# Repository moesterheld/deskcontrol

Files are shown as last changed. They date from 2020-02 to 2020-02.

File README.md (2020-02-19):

# myDeskControl Steuerung
## Wofür ist myDeskControl?
myDeskControl ist eine Arduino basierte Erweiterung für Assmann Sympas Steh-Sitz-Tische. Sie wird zwischen die Steuerknöpfe am Tisch und die Steuereinheit unter dem Tisch geschaltet und kann so die Steuerung des Motors automatisieren. Durch Nutzung eines Ultraschalldistanzsensors können so eine Position für Oben und Unten gespeichert und angesteuert werden. 
## Wie wird myDeskControl benutzt?
An die myDeskControl Einheit wird das bestehende Anschlusskabel der Steuerungsknöpfe angeschlossen um auf Tastendrücke reagieren zu können. Die Tastendrücke werden dann verarbeitet und über ein an die bestehende Buchse der Steuereinheit des Motors angeschlossenes Netzwerkkabels die notwendigen Aktionen ausgeführt.
Dabei können folgende Funktionen über die Tasten angesteuert werden:
- Langer Druck auf :heavy_plus_sign: / :heavy_minus_sign: : Tisch auf- / abfahren (entspricht der Standardfunktion)
- Druck auf :heavy_plus_sign: direkt gefolgt von einem Druck auf :heavy_minus_sign: : Aktuelle Position als "Oben" Position speichern
- Druck auf :heavy_minus_sign: direkt gefolgt von einem Druck auf :heavy_plus_sign: : Aktuelle Position als "Unten" Position speichern
- Kurzer Druck auf :heavy_plus_sign: / :heavy_minus_sign: : Tisch automatisch zu gespeicherter Position auf- / abfahren
- Durch den Druck auf eine der Tasten während der automatischen Fahrt kann die Fahrt gestoppt oder eine automatische Fahrt in die andere Richtung ausgelöst werden.  
## Wie funktioniert myDeskControl?
myDeskControl verwendet als zentrales Bauteil einen Arduino (kompatiblen) Mikroprozessor. 
Da die Steuertasten des Tisches über ein RJ45 Kabel an der Tischsteuerung angeschlossen sind, kann der Anschluss zur Erkennung am Mikroprozessor relativ einfach erfolgen. 
Zur Positionsmessung ist ein Ultraschallsensor am Mikroprozessor angeschlossen, der bei Bedarf die aktuelle Entfernung zum Boden misst.  
Aus Tastendruck und aktueller Position kann der Prozessor berechnen, welche Aktion zum Erreichen der gewünschten Funktionalität notwendig ist. Diese Aktion wird durch eine Simulation des Tastendrucks ausgeführt.
Die Tastendrücke zum Hoch-/Runterfahren des Tisches werden durch je einen Optokoppler der das Signal dann wieder über ein RJ45 Kabel an die Steuereinheit überträgt simuliert.
Durch Betätigen beider Tasten gleichzeitig kann die aktuelle Position als Oben-/Unten-Position persistent im EEPROM des Mikroprozessors gespeichert werden und steht so auch noch zur Verfügung nachdem die myDeskControl vom Strom getrennt wurde.  
Eine maximale Fahrzeit in eine Richtung dient als Sicherungsfunktion um nicht unter Umständen (z.B. bei Defekt eines der Tasten) unkontrolliert in eine Richtung zu fahren. Alle weiteren von Werk integrierten Sicherungsfunktionen des Tisches (Maximalhöhe / Blockierungsschutz) bleiben erhalten.
## Wie kann ich mir mein eigenes myDeskControl bauen?
Für den Bau des myDeskControl werden benötigt:
- 1x [Wemos D1 Mini ESP8266-12F Mikroprozessor](https://amzn.to/37IjiAW)
- 1x [HC-SR04 Ultraschall Sensor](https://amzn.to/37GAg2z)
- 2x [RJ45 Buchse](https://amzn.to/2udEeCb)
- 2x [PC817 Optokoppler](https://amzn.to/2HF5MmR)
- 4x 220&#8486; Widerstand
- 4x 10k&#8486; Widerstand
- 2x LEDs
- 1x passende Lochrasterplatine oder alternativ die von aisler.com produzierte Platine aus dem Fritzing Entwurf.

Aus Platz- und Kostengründen wird für das veröffentlichte Projekt auf einen Wemos D1 Mini ESP8266 Mikroprozessor zurückgegriffen. Die Funktionalität kann aber für jeden Arduino-kompatiblen Mikroprozessor angepasst werden.

Auf die beiden LEDs sowie zwei der zugehörigen 220&#8486; Vorwiderstände kann verzichtet werden. Sie dienen lediglich der optischen Anzeige der aktuell betätigten Fahrtrichtung. Zusätzlich wird das Speichern der Position als Blinken angezeigt.

Der Anschluss erfolgt gemäß dem [Fritzing Entwurfs](DeskControlDeluxe.fzz) als Prototyp

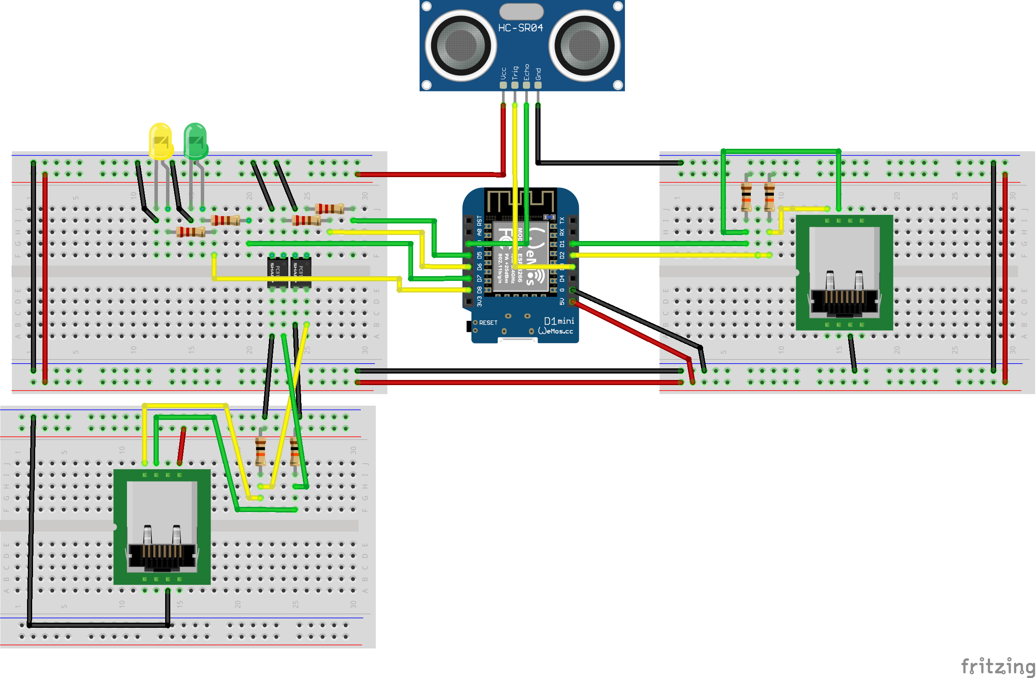
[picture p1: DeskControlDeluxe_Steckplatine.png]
Prototype


oder auf der Leiterplatte

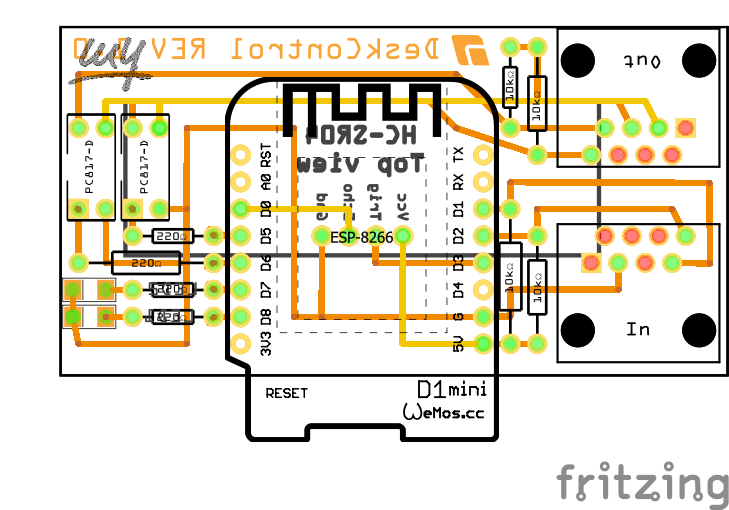
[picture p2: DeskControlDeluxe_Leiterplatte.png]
Leiterplatte


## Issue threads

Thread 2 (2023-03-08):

Research Protokoll hinterer RJ45

peteh, 2023-03-08:
Hi,

mein Tisch hat 2 RJ45 Stecker, kann man darueber auch komplexere Befehle senden oder ist das ganze wirklich nur ein Mapping auf digitale IOs?
Es gibt ein Tool von OMT, mit dem man den Tisch auch per USB  vom PC kontrollieren kann.

moesterheld, 2023-03-08:
Hi @peteh, ich hatte nur die einfachen Auf-/Ab Schalter zur Verfügung und festgestellt, dass sie ganz gewöhnliche Schalter, die über die drei Adern im RJ45 schalten. Das habe ich mir damals für das Projekt zunutze gemacht.
Ich denke aber schon, dass man damit auch komplexer steuern könnte, wenn man ein "richtiges" Steuergerät reengineeren würde oder die Specs kennen würde. Da kann ich aber leider nicht weiterhelfen, da mir das abgeht und ich mittlerweile nicht einmal mehr Zugriff auf einen dieser Tische habe.

Closed 2023-03-08.

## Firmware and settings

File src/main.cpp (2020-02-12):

#include <Arduino.h>
#include <EEPROM.h>
#include <MyUltrasoundSensor.h>

// pins
int BUTTON_UP = D1;   // pull-up !
int BUTTON_DOWN = D2; // pull-up !
int US_TRIGGER = D3;
int US_ECHO = D0;
int OUTPUT_UP = D6;
int OUTPUT_DOWN = D5;
int LED_UP = D7;
int LED_DOWN = D8;

// variables for button logic
enum direction {
  NONE, UP, DOWN
};
enum mode {
  MANUAL, AUTOMATIC
};
direction initialDirection = NONE;
bool buttonPressed = false;
bool buttonLongPressed = false;
bool positionStored = false;
uint32_t  buttonTimer = 0;
uint32_t  longPressTimeout = 1000;

// variables for driving desk
MyUltrasoundSensor uss(US_TRIGGER, US_ECHO);
int lastPosition;
int positionUp;
int positionDown;
int EEPROM_UP = 0;
int EEPROM_DOWN = 1;
direction drivingDirection = NONE;
mode drivingMode = MANUAL;
uint32_t  drivingTimer = 0;
uint32_t  drivingTimeout = 20000;

// stop driving desk
void stopDesk() {
  Serial.println("Stopping desk");
  // stop motor
  digitalWrite(OUTPUT_UP, LOW);
  digitalWrite(LED_UP, LOW);
  digitalWrite(OUTPUT_DOWN, LOW);
  digitalWrite(LED_DOWN, LOW);
  drivingDirection = NONE;
  drivingMode = MANUAL;
}

// start driving desk in direction
void driveDesk(direction dir) {
  // drive motor in direction (stop going the other way first)
  if (drivingDirection != NONE && drivingDirection != dir) {
    stopDesk();
  }
  if (drivingDirection == NONE) {
    drivingTimer = millis();
  }
  if (drivingDirection == dir) {
    return;
  }
  if (dir == UP) {
    Serial.println("Driving desk up");
    digitalWrite(OUTPUT_UP, HIGH);
    digitalWrite(LED_UP, HIGH);
    drivingDirection = UP;
  } else {
    Serial.println("Driving desk down");
    digitalWrite(OUTPUT_DOWN, HIGH);
    digitalWrite(LED_DOWN, HIGH);
    drivingDirection = DOWN;
  }
}

// start autodriving desk to position
void autoDriveDesk(direction dir) {
  // auto drive desk to position, stop motor if already going in that direction
  if (drivingDirection != NONE && drivingDirection == dir) {
    stopDesk();
    return;
  } 

  if ((dir == UP && lastPosition >= positionUp) || (dir == DOWN && lastPosition <= positionDown)) {
    Serial.println("Not driving desk. Already in position.");
    return;
  }

  Serial.print("Driving desk to position ");
  if (dir == UP) {
    Serial.println("UP");
  } else {
    Serial.println("DOWN");
  }
  drivingMode = AUTOMATIC;
  driveDesk(dir);
}

void blink(int ledPin) {
  for (int i=0; i<3; i++) {
    digitalWrite(ledPin, HIGH);
    delay(200);
    digitalWrite(ledPin, LOW);
    if (i<2) {
      delay(200);
    }
  }
}

// store position to eeprom
void writeToEeprom(int position, direction dir) {
  position = (position < 0 || position > 255) ? 100 : position;
  EEPROM.begin(2);
  if (dir == UP) {
    Serial.print("Storing position UP: ");
    if (position != EEPROM.read(EEPROM_UP)) {
      Serial.print("*new* ");
      EEPROM.write(EEPROM_UP, position);
    }
    blink(LED_UP);
    positionUp = position;
  } else {
    Serial.print("Storing position DOWN: ");
    if (position != EEPROM.read(EEPROM_DOWN)) {
      Serial.print("*new* ");
      EEPROM.write(EEPROM_DOWN, position);
    }
    blink(LED_DOWN);
    positionDown = position;
  }
  EEPROM.commit();
  Serial.println(position);
}

// read up and down positions from eeprom and store in global variables
void readPositions() {
  EEPROM.begin(2);
  Serial.println("Reading positions from EEPROM");
  positionUp = EEPROM.read(EEPROM_UP);
  positionDown = EEPROM.read(EEPROM_DOWN);
  EEPROM.end();
  Serial.print("Position UP: ");
  Serial.println(positionUp);
  Serial.print("Position DOWN: ");
  Serial.println(positionDown);
}

// measure position in cm using HC-SR04
int measure() {
  // Clears the trigPin
  digitalWrite(US_TRIGGER, LOW);
  delayMicroseconds(2);
  // Sets the trigPin on HIGH state for 10 micro seconds
  digitalWrite(US_TRIGGER, HIGH);
  delayMicroseconds(10);
  digitalWrite(US_TRIGGER, LOW);
  // Reads the echoPin, returns the sound wave travel time in microseconds
  long duration = pulseIn(US_ECHO, HIGH);
  // Calculating the distance
  int distance = duration*0.034/2;
  return distance;
}

int measurePosition() {
  int distance = uss.distanceTempCompMedian(20);
  Serial.print("Current position: ");
  Serial.println(distance);
  lastPosition = distance;
  return distance;
}
 
// measure and store current position for given direction
void storePosition(direction dir) {
  if (!positionStored) {
    int position = measurePosition();
    position = (position > 255) ? 255 : (position < 0) ? 0 : position;
    writeToEeprom(position, dir);
  }
  positionStored = true;
}

// run when button press is started
void initializeButtonPress(direction dir) {  
  Serial.print("Button pressed: ");
  if (dir == UP) {
    Serial.println("UP");
  } else {
    Serial.println("DOWN");
  }
  buttonPressed = true;
  buttonTimer = millis();
  initialDirection = dir;
}

void setup() {
  pinMode(BUTTON_UP, INPUT);
  pinMode(BUTTON_DOWN, INPUT);
  pinMode(OUTPUT_UP, OUTPUT);
  pinMode(OUTPUT_DOWN, OUTPUT);
  pinMode(LED_UP, OUTPUT);
  pinMode(LED_DOWN, OUTPUT);
  Serial.begin(9600);
  readPositions();
  uss.medianNumber = 3;
  uss.measureDelay = 30;
  measurePosition();
}

void loop() {

  if (digitalRead(BUTTON_UP) == LOW) { 
    if (!buttonPressed) {
      initializeButtonPress(UP);
    } else if (!buttonLongPressed && initialDirection == DOWN) {
      storePosition(initialDirection);
    }
  }  

  if (digitalRead(BUTTON_DOWN) == LOW) { 
    if (!buttonPressed) {
      initializeButtonPress(DOWN);
    } else if (!buttonLongPressed && initialDirection == UP) {
      storePosition(initialDirection);
    }
  }  

  if (buttonPressed && ((millis() - buttonTimer) > longPressTimeout) 
      && !buttonLongPressed && !positionStored) { // long press button
    buttonLongPressed = true;
    driveDesk(initialDirection);
  }

  if (digitalRead(BUTTON_UP) == HIGH && digitalRead(BUTTON_DOWN) == HIGH) { // button release, react to short press and do long press end
    if (buttonPressed) {
      if (buttonLongPressed) {
        buttonLongPressed = false;
        stopDesk();
        measurePosition();
      } else if (!positionStored) {
        autoDriveDesk(initialDirection);
      }
      initialDirection = NONE;
      buttonPressed = false;
      positionStored = false;
    }
  }

  if (drivingDirection != NONE) {
    if ((millis() - drivingTimer) > drivingTimeout) {
      Serial.println("ERROR: Driving timeout reached!");
      stopDesk();
    } else if (drivingMode == AUTOMATIC) {
      long currentPosition = measurePosition();
      if (drivingDirection == UP && currentPosition >= positionUp) {
        Serial.println("UP Position reached!");
        stopDesk();
      } else if (drivingDirection == DOWN && currentPosition <= positionDown) {
        Serial.println("DOWN Position reached!");
        stopDesk();
      }
    }
  }

}

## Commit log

2020-01-17 switch to platform, remove unsigned int warning
2020-01-20 add led output, debug messages
2020-01-27 Fritzing Diagram
    [DeskControl.fzz]
2020-01-30 Platinenansicht upgedated
    [DeskControl.fzz]
2020-01-30 Logo und Beschriftungen hinzugefügt
    [DeskControl.fzz]
2020-01-30 Deluxe Version mit RJ45 Output
    [DeskControlDeluxe.fzz]
2020-02-12 Update Pinout für AIsler Platine
    [DeskControlDeluxe.fzz]
